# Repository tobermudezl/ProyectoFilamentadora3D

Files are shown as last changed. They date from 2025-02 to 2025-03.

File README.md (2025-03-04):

# ProyectoFilamentadora3D
Proyecto para la materia de Taller de Ingenieria Electronica.

# Integrantes 
Tomás Bermudez Lozano         | tobermudezl@unal.edu.co 

Juan Esteban Martinez Leon    | jumartinezle@unal.edu.co

Brayan Santiago Celi Almanza  | bceli@unal.edu.co

Johan Steven Ruiz Arango      | joruizar@unal.edu.co

# Descripción

Nuestro Proyecto tiene como fin de usar plastico reciclado filetiado (crear tiras homogeneas de plastico PET) por el usuario con el fin de crear filamento 3D con un prototipo economico y rentable para quienes quieran idearlo. Principalmente fue pensado para un consumo y reutilizacion eficaz de nuestros desechos plasticos. Los mismos desechos que se demoran al rededor de 300 o 400 años en descomponerse completamente. Aprovechando ese "problema" podemos verlo como una solucion eficaz para crear objetos en plastico resistentes, duraderos y amigables con el medio ambiente. Es un prototipo que tiene planeado ser implementado cerca de las salas con impresoras 3D con el fin que loe estudiantes puedan usar sus propias botellas plasticas recicladas y previamente fileteadas para poder ser introducidas por el prototipo y previamente usar el filamento 3D para sus proyectos.

# Problematica 

En Bogotá, la situación de los residuos plásticos es un desafío que afecta a todos. A medida que la ciudad crece y se urbaniza, también lo hacen los desechos plásticos, los cuales terminan, en su mayoría, en vertederos, ríos o incluso en las calles, generando problemas de contaminación que afectan la salud y el bienestar de los bogotanos. Aunque se han realizado esfuerzos por mejorar la gestión de residuos, todavía muy poco de lo que se produce se recicla correctamente, lo que agrava la situación y contribuye al cambio climático.
Por otro lado, la impresión 3D, que está ganando terreno en Bogotá, ofrece un sinfín de posibilidades en áreas como la educación, la construcción y la innovación tecnológica. Sin embargo, esta tecnología depende de filamentos plásticos, los cuales, en su mayoría, provienen de materiales nuevos, lo que continúa alimentando la demanda de recursos no sostenibles y aumentando el impacto ambiental. Aunque existen algunas alternativas de reciclaje, las tecnologías actuales para convertir los plásticos en nuevos productos no se han masificado por su alto costo y lo complejas que son de implementar. Es aquí donde surge una gran oportunidad: crear soluciones innovadoras que no solo ayudan a reducir los residuos plásticos, sino que también promuevan un uso más responsable de estos materiales, especialmente en áreas como la impresión 3D. Imaginemos una máquina capaz de transformar los plásticos que generamos en filamentos reciclados que puedan ser utilizados nuevamente para crear productos. Esta máquina no solo ayudaría a disminuir la cantidad de plásticos que terminan en vertederos, sino que también contribuiría a crear un ciclo de reutilización, donde los plásticos reciclados puedan tener una nueva vida, reduciendo la necesidad de plásticos vírgenes.
El agregado de un sistema de monitoreo en tiempo real permitiría controlar el proceso de reciclaje, asegurando que el filamento reciclado cumpla con los estándares necesarios para su uso en impresión 3D. Esto garantizaría que, incluso con plásticos reciclados, se mantuviera la calidad y funcionalidad del material. Implementar esta solución en Bogotá tendría múltiples beneficios. Por un lado, ayudaría a disminuir la cantidad de plástico desperdiciado que afecta tanto al medio ambiente como a la calidad de vida de los ciudadanos. Además, al reutilizar estos materiales, contribuiremos al cuidado del entorno y a reducir el impacto ambiental de la ciudad. Pero no solo eso, también abriría nuevas oportunidades de negocio, generando empleo en áreas como el reciclaje y la producción de materiales ecológicos. De esta manera, Bogotá podría fortalecer su compromiso con la sostenibilidad y avanzar hacia un futuro más verde y responsable.
Con proyectos como este, Bogotá podría dar un gran paso hacia un modelo más sostenible, no solo para enfrentar los problemas de los plásticos, sino para transformar la ciudad en un referente de innovación ambiental. Al integrar tecnologías como el reciclaje inteligente y la producción de filamentos reciclados, podríamos crear una economía más circular, generar empleo y, lo más importante, mejorar la calidad de vida para todos los bogotanos

# Objetivos 

Desarrollar un prototipo de filamentadora con método de extrusión sostenible a partir de residuos plásticos PET, que integre un sistema de monitoreo en tiempo real basado en IoT para garantizar la calidad del filamento producido, contribuyendo a la economía circular y la sostenibilidad ambiental.

# Objetivos Especifico

..* Diseñar el prototipo de la filamentadora con sistema de extrusión para el reciclaje de plásticos PET. 
..* Implementar un sistema de monitoreo en tiempo real mediante sensores IoT para la supervisión de la temperatura
..* Evaluar la calidad del filamento producido en términos de uniformidad, resistencia y viabilidad para la impresión 3D.
..* Desarrollar una interfaz gráfica para la visualización remota de los datos obtenidos por los sensores. 
..* Promover la conciencia ambiental sobre la reutilización de residuos plásticos a través de la demostración y divulgación del prototipo.

# Cronograma

![alt text]()

# Poster
![Poster]

# Producto Final

![Video Producto Final]

# Palabras Claves

Prototipos, Plastico reciclado, filamentadora, universidad, PET, plastico, reciclaje, medio ambiente.

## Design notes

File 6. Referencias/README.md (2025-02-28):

# Planteamiento de la Idea 

[Idea de la Filamentadora 3D](https://youtu.be/36BITwMVMGE?si=6mY6h9IGPmX1kqub)

Este fue el primer video que vimos como idea inicial, sabiendo que nuestro prototipo no se guiaria en todo lo que vimos, si no que es la idea principal.

# Videos para saber cosas que no teniamos ni idea de hacer 

[Como usar un motor paso a paso con ESP32](https://www.youtube.com/watch?v=MP3kUJ6SFCQ)

[Conectarlo con wifi el funcionamiento del motor paso a paso](https://www.youtube.com/watch?v=ysoVaclMy9Y)

[Motor PASO A PASO con ULN2023A Driver](https://www.youtube.com/watch?v=wLdFx4Kgc4M)

# Esquemas de conexion

## Esquema de conexion del sensor de temperatura DS18B20 con el microcontrolador ESP32

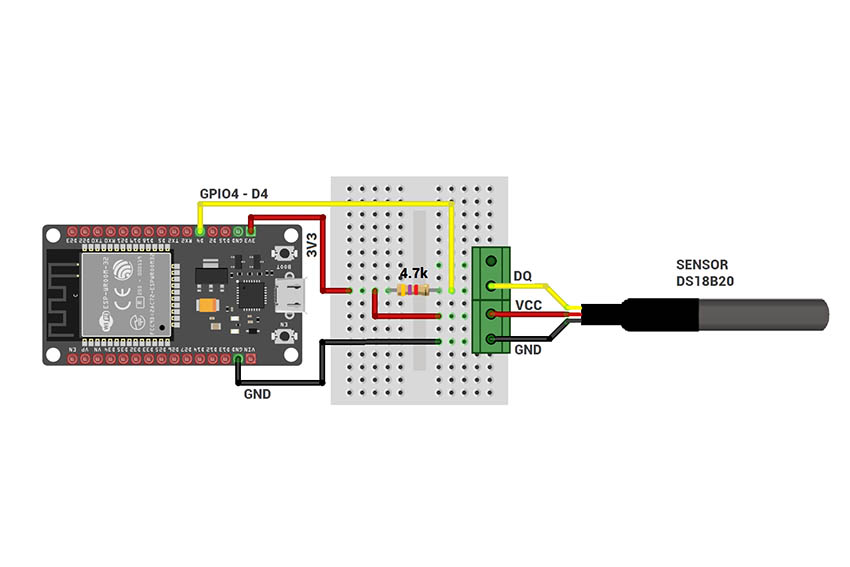
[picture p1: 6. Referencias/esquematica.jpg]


## PinOUT de ESP32 WROOM DEVKITV1

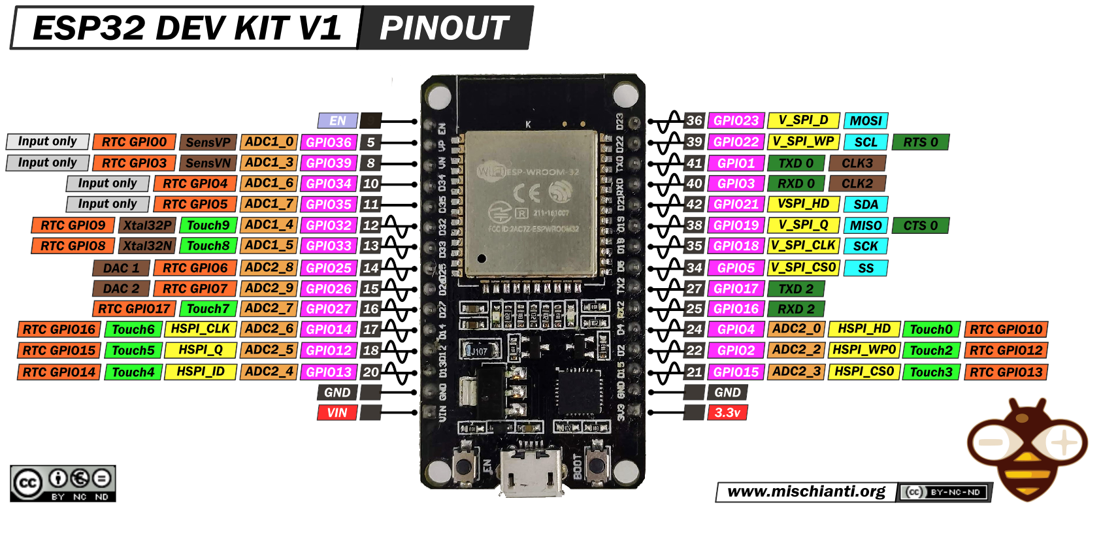
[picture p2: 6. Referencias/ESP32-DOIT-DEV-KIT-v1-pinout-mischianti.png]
esp32


## Conexion del LM7805

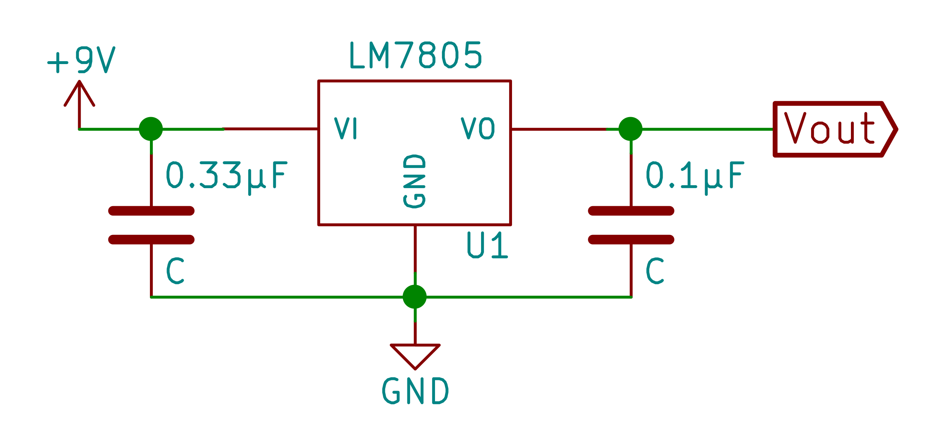
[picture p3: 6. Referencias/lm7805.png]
adap


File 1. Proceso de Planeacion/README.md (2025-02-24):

# Requerimientos

En esta parte comenzamos a pensar lo que queremos como proyecto final, nuestra idea principal de que queremos que nuestro prototipo haga, calcule, muestre, informe. Queremos que sea intregado con IoT porque es algo muy loco que nos enseño el Profe Johnny desde la primera clase. 

En el siguiente link se podra observar el PDF donde estan todas estas informaciones a detalle :) [REQUERIMIENTOS PRESENTACION](https://github.com/tobermudezl/ProyectoFilamentadora3D/blob/main/1.%20Proceso%20de%20Planeacion/Requerimientos.pdf)
# Diagrama de Flujo
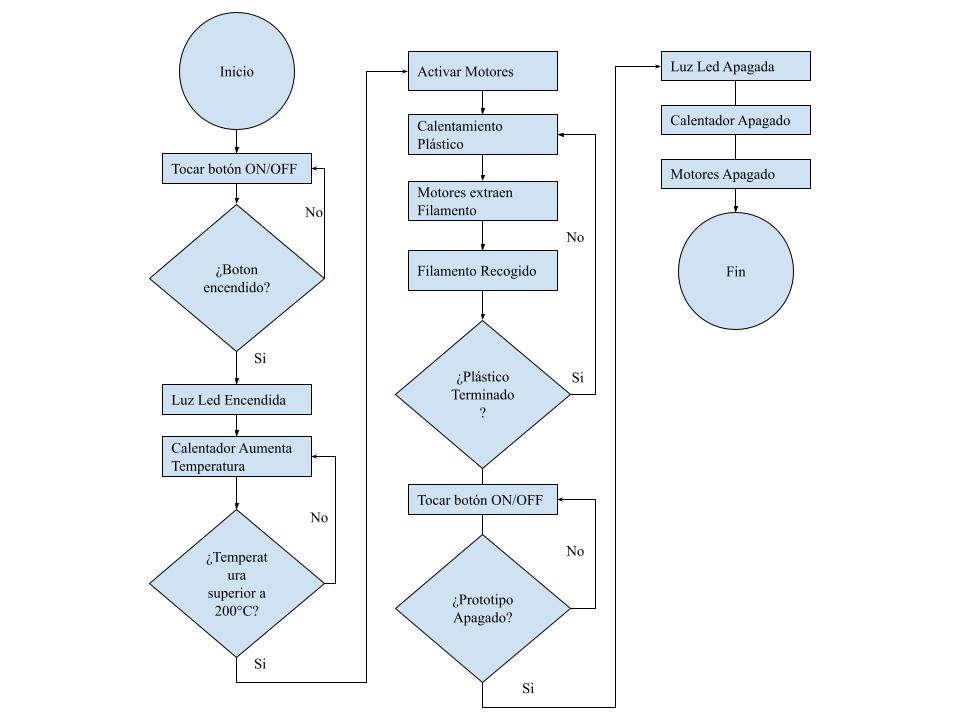
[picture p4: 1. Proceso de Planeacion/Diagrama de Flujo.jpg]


# Diagrama de Caja Negra - Sin tecnologia

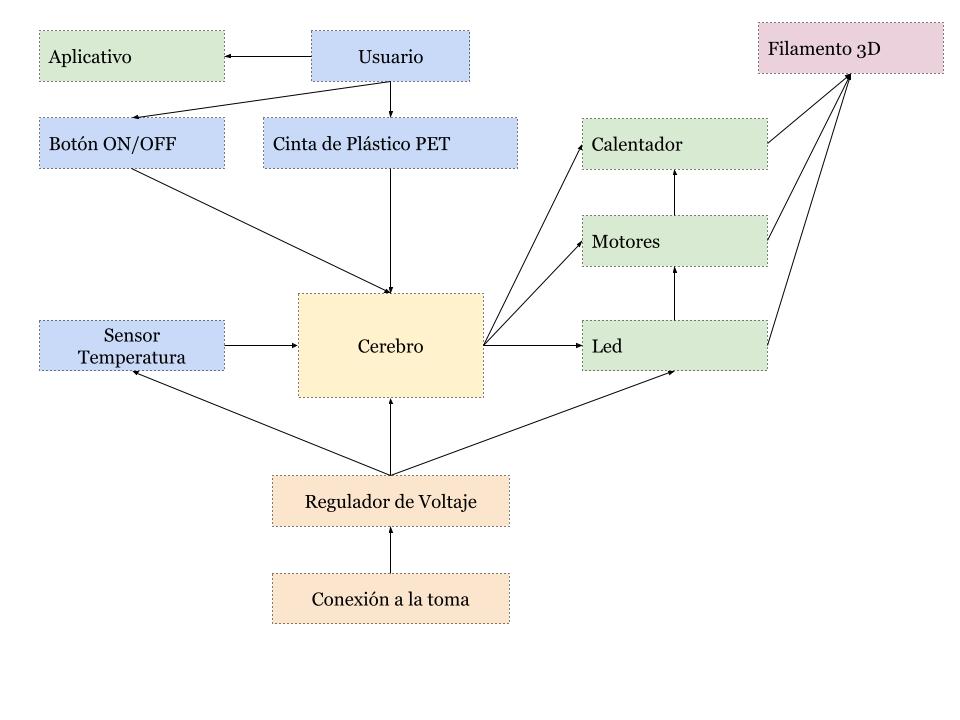
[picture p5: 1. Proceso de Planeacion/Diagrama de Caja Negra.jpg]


# Lista de Materiales

| **Material** | **Cantidad**  | 
| --- |:---:|
| Motores PASO A PASO28BYJ8 | 2 |  
| ULN2003A | 2 | 
| Condensadores de 10mf | 2 | 
| Resistencia de 4.7K ohm | 1 |  
| ESP32 DEV KIT V1 DOIT | 1 |
| Resistencia ceramica 40W | 1 |
| Parte calentador plastico | 1 |
| Led Verde | 1 |
| Resistencia  520 ohm | 1 | 
| LM7805 Regulador Voltaje | 1 |
| Cables o Jumpers | |

# Diagrama de Caja Negra - Con tecnologia

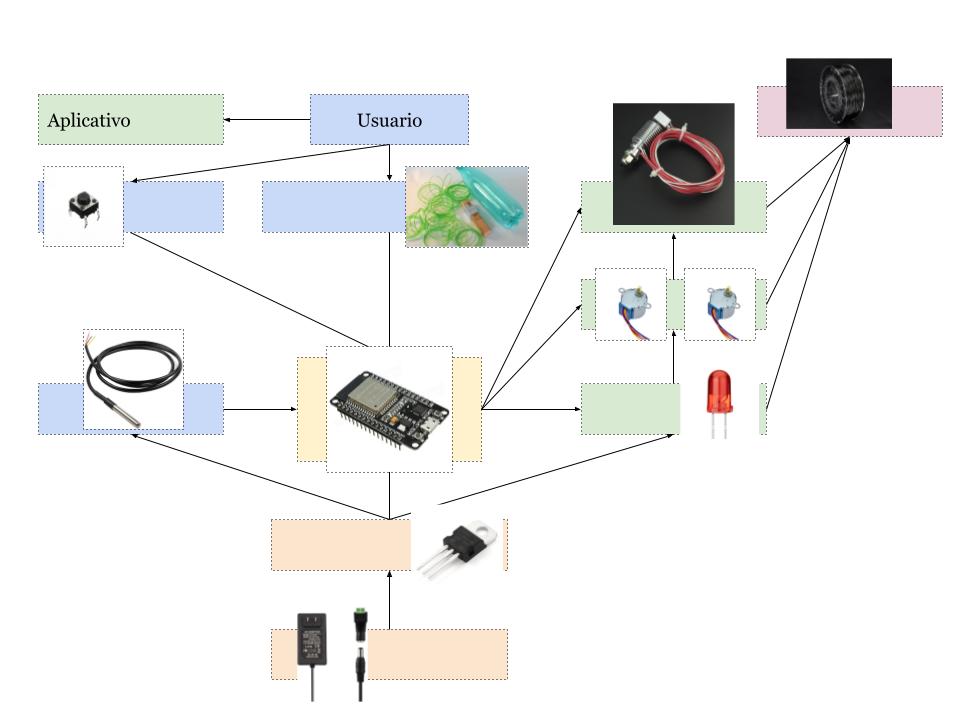
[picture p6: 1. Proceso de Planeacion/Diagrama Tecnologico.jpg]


# Paso a la fase 2

Despues de todo planificado pasamos a la parte dos del proyecto.

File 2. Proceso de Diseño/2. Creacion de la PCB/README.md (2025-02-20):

#  Informacion de la PCB

Una PCB de 9x9, una capa, tarjeta de fibra, antisolder, serigrafia.

Se ponen en esta carpeta las librerias usadas, los archivos completos del proyecto en KiCad.

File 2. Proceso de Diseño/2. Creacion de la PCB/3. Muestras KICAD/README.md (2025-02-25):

# Muestras Rapidas de Archivos KICAD

Primero tenemos el esquematico completo en pdf : [Esquematico](https://github.com/tobermudezl/ProyectoFilamentadora3D/blob/main/2.%20Proceso%20de%20Diseño/2.%20Creacion%20de%20la%20PCB/3.%20Muestras%20KICAD/esquematico.pdf)

La foto del ruteo de la PCB

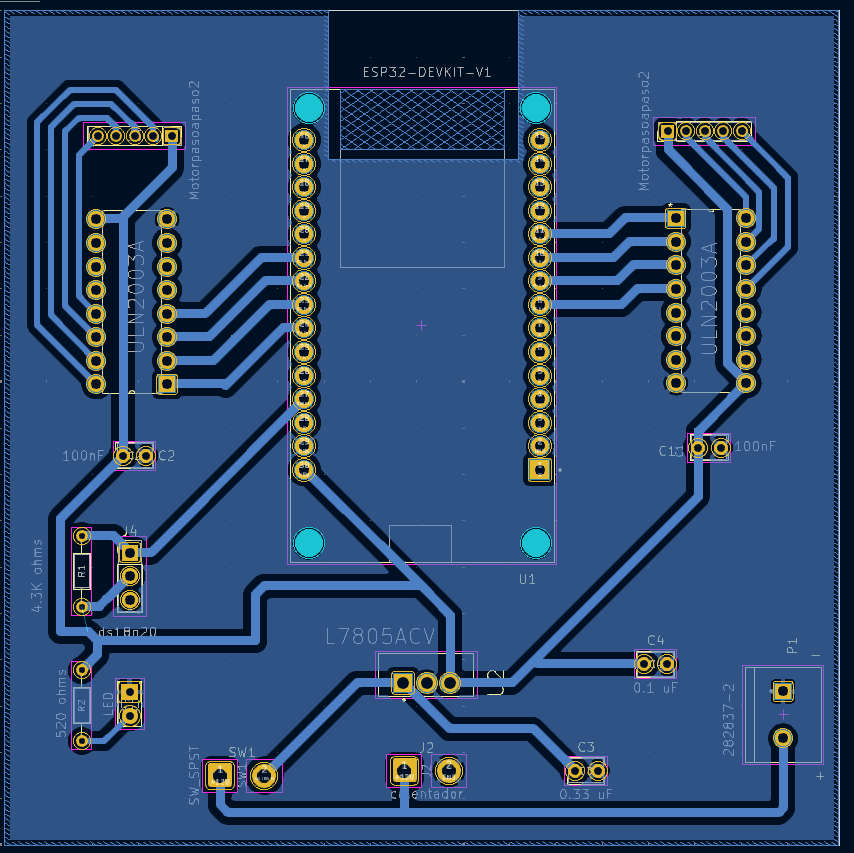
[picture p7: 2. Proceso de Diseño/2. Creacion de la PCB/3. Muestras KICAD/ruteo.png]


Y la foto de como se veria el modelo en version 3D

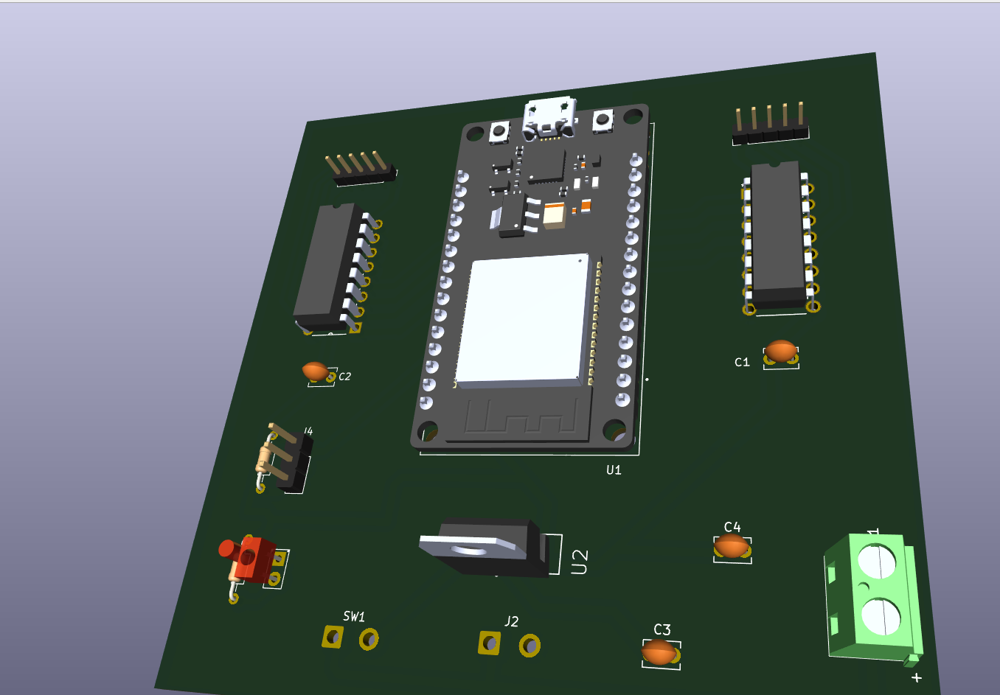
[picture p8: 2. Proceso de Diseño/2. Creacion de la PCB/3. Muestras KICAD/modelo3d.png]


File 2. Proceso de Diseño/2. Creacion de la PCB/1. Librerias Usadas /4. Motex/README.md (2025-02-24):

# Librerias de MOTEX

Incluye el archivo .kicad_sym, .step y .kicad_mod

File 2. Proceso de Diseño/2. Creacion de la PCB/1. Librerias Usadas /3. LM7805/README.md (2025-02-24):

# Librerias de LM7805 

Incluye el archivo .kicad_sym, .step y .kicad_mod

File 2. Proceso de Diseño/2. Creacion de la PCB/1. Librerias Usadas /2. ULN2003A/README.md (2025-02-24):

# Librerias de ULN2003A 

Incluye el archivo .kicad_sym, .step y .kicad_mod

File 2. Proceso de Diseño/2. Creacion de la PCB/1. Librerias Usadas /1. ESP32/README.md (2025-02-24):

# Librerias de ESP32 

Incluye el archivo .kicad_sym, .step y .kicad_mod

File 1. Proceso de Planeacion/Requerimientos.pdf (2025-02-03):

# REQUERIMIENTOS

## GRUPO 2

# Situación problema

La creciente utilización de plásticos de un solo uso, que en su mayoría no son reciclados adecuadamente, termina acumulándose en rellenos sanitarios como el de Doña Juana en Bogotá. Este relleno recibe alrededor de 300 toneladas de basura, de las cuales aproximadamente el 40 % corresponde a plásticos.

Nuestro prototipo está diseñado para aprovechar estos plásticos, específicamente el PET (#1), transformándolos en filamento para impresoras 3D. Este filamento permitirá la impresión de objetos que fomenten el reciclaje individual, promoviendo así la reutilización de plásticos de un solo uso y contribuyendo a una gestión más sostenible de los residuos.

# Flujo de Proceso

Proceso Previo: Antes de utilizar la máquina, el usuario debe triturar el plástico PET. Esto puede realizarse con herramientas accesibles, como una licuadora convencional, asegurándose de que los fragmentos sean lo suficientemente pequeños para ser procesados por el sistema.

# Flujo de Proceso

Etapas del Proceso:

1. Entrada: Se introduce plástico triturado por el usuario en el sistema a través de una tolva o compartimiento diseñado para este propósito.
2. Fusión: El plástico es calentado hasta alcanzar la temperatura ideal para su fundición, evitando la degradación del material y preservando su calidad.
3. Extrusión: El material fundido es moldeado mediante un cabezal de extrusión, formando un filamento uniforme con el diámetro requerido.
4. Enfriamiento: El filamento extruido pasa a través de un sistema de enfriamiento controlado para solidificarse sin deformaciones.
5. Enrollamiento: El filamento enfriado es automáticamente enrollado en bobinas, asegurando un almacenamiento práctico y listo para su uso en impresoras 3D.

# Funcionales

Procesamiento de plásticos: Debe fundir el PET triturado y moldearlo en filamentos de un diámetro adecuado para impresoras 3D.
Producción de filamento: El sistema debe tener el grosor del filamento para asegurar compatibilidad con estándares de impresoras 3D. Al igual debe embobinar el filamento producido para facilitar su uso.
Soporte para impresión 3D: Los filamentos producidos deben ser compatibles con las impresoras 3D más comunes en el mercado. Igualmente debe permitir la creación de objetos reutilizables o piezas relacionadas con el reciclaje. Monitoreo y reporte: El sistema debe permitir monitorear la temperatura y el correcto funcionamiento, al igual de poder dar un reporte completo.

# No funcionales

Eficiencia Energética: El sistema debe optimizar el consumo de energía durante todo el proceso.
Facilidad de Uso: La operación del sistema debe ser intuitiva y accesible para usuarios con diferentes niveles de experiencia, incluso sin conocimientos técnicos avanzados.De la misma forma la interfaz debe incluir instrucciones claras y herramientas automatizadas para reducir la intervención manual.
Portabilidad: El sistema debe tener un diseño compacto y modular, facilitando su transporte e instalación en distintos lugares, como centros de reciclaje comunitarios o pequeñas empresas.
Seguridad: Advertencias del uso del prototipo para evitar quemaduras, malos usos, y sus especificaciones para poder darle un manejo completo.

# No funcionales

Materiales Accesibles: El diseño del sistema debe priorizar componentes y materiales que sean fáciles de conseguir en el mercado local y que no encarezcan su producción. Siempre que sea posible, debe incluir materiales reciclados o reutilizables en su construcción.
Durabilidad: El sistema debe estar construido con materiales resistentes al desgaste, garantizando una vida útil prolongada incluso bajo condiciones de uso continuo.
Bajo Coste de Producción: Los costos asociados al desarrollo y operación del sistema deben mantenerse bajos para asegurar su viabilidad económica. Esto incluye el uso eficiente de recursos, la optimización del diseño y la reducción de desperdicios durante el proceso de fabricación.

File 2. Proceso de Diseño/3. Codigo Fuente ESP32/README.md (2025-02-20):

# Codigo Fuente del programa principal

Se adjuntaran los codigos de prueba y el main completo

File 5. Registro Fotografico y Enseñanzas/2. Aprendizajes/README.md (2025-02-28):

# Reflexión del Proceso de Aprendizaje

Como grupo, hemos vivido un proceso de aprendizaje donde la autonomía y el acompañamiento del profesor Johnny jugaron un papel fundamental. A lo largo del camino, enfrentamos diversos errores en diferentes aspectos, desde la planificación hasta la implementación. Cada equivocación fue una oportunidad para mejorar, buscando soluciones de forma colaborativa, investigando por nuestra cuenta y con el apoyo del profesor.

Entendimos que cometer errores es parte esencial del aprendizaje, ya que nos permitió fortalecer nuestros conocimientos, desarrollar paciencia y crecer como equipo. Gracias a cada desafío superado, hoy somos mejores que cuando iniciamos, y nos llevamos la enseñanza de que los errores no son fracasos, sino pasos necesarios para alcanzar el aprendizaje.

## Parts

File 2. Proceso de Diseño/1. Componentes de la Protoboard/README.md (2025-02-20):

# Elementos usados para el prototipo

En nuestro proyecto usamos varios materiales :

El Calentador de plastico :

![alt]()

Motores Paso A Paso :

![alt]()

ULN2003A :

![alt]()

Resistencias :

![alt]()

LM7805 :

![alt]()

Capacitores 104 (100nF):

![alt]()

ESP32 DEVKIT V1 :

![alt]()

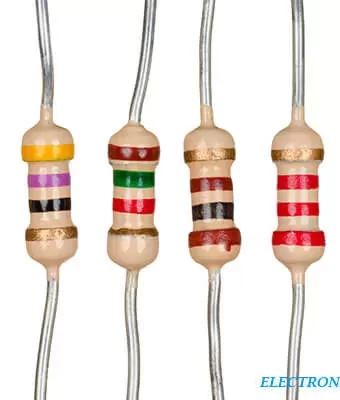
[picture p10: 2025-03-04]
2. Proceso de Diseño/1. Componentes de la Protoboard/res.webp

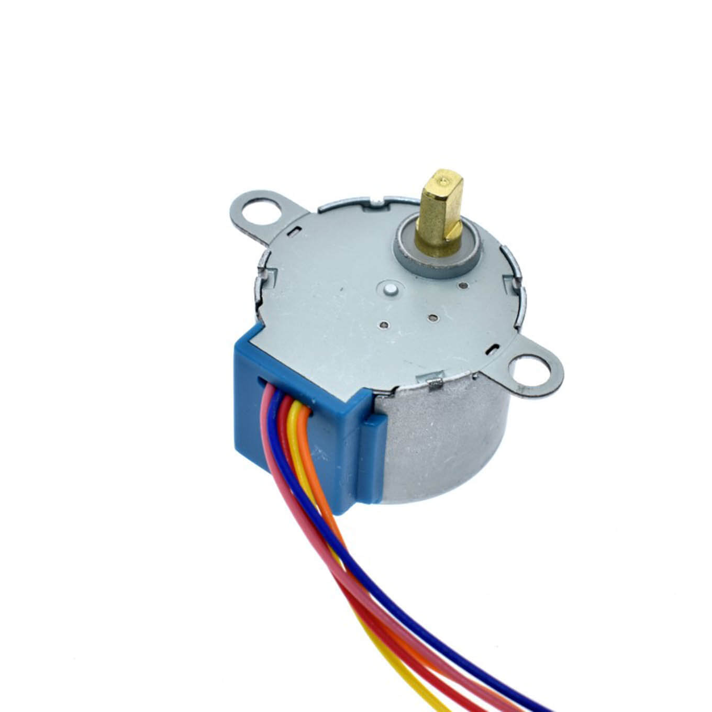
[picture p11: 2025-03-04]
2. Proceso de Diseño/1. Componentes de la Protoboard/motor.jpg

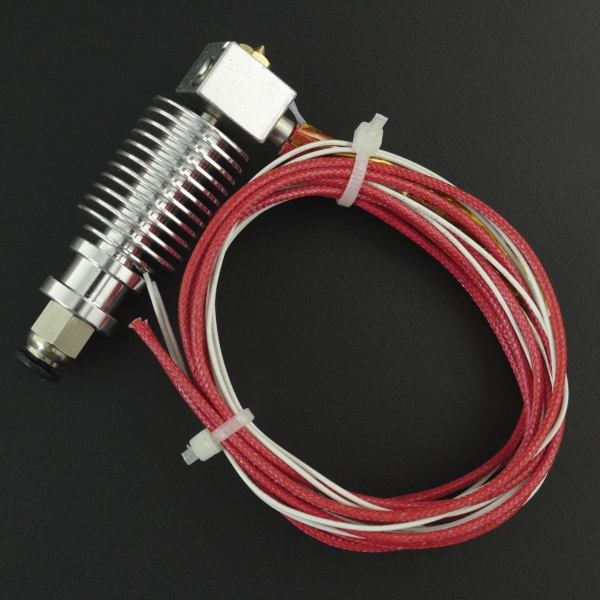
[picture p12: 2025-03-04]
2. Proceso de Diseño/1. Componentes de la Protoboard/extructor.jpg

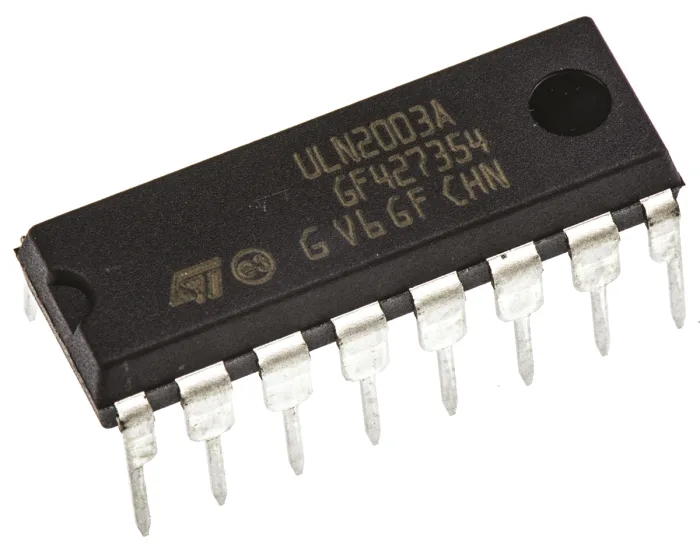
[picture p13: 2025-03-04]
2. Proceso de Diseño/1. Componentes de la Protoboard/uln2003a.webp

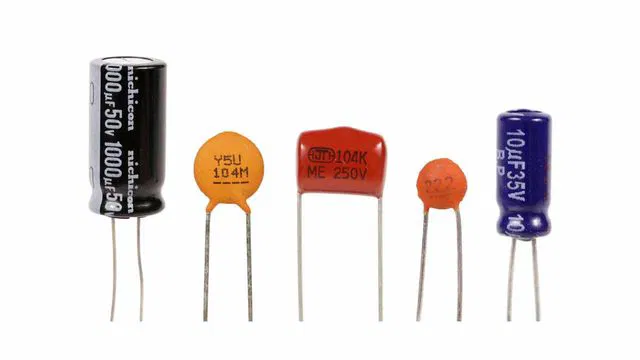
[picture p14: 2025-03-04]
2. Proceso de Diseño/1. Componentes de la Protoboard/capacitor.webp

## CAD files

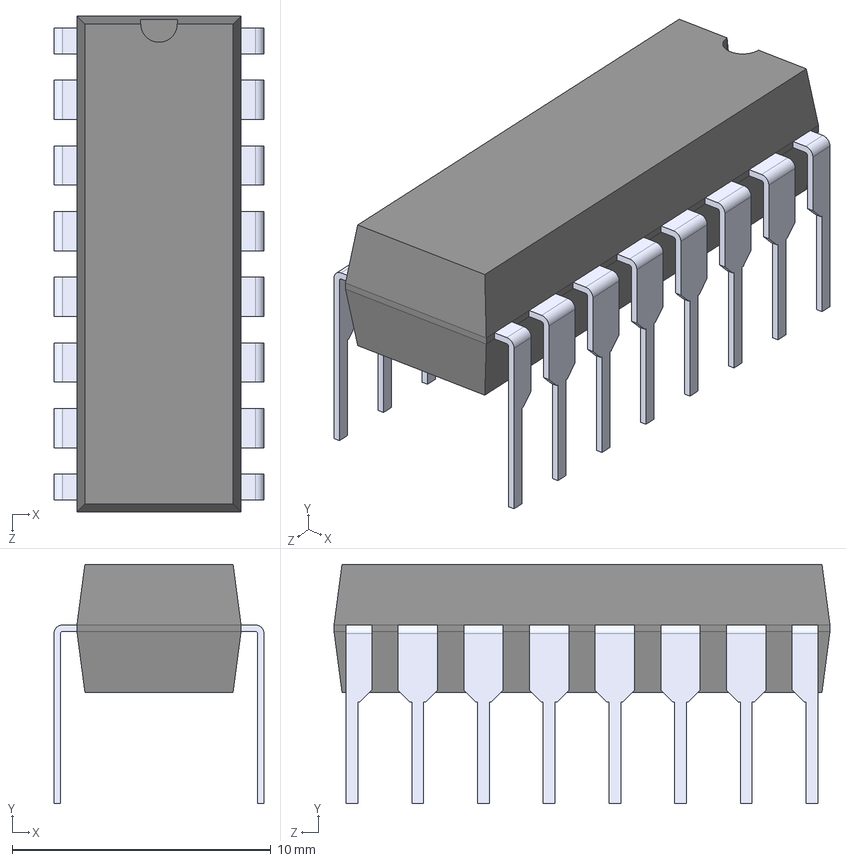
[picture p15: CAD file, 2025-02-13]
2. Proceso de Diseño/2. Creacion de la PCB/1. Librerias Usadas /2. ULN2003A/ULN2003A.step
8.12 x 9.26 x 19.2 mm

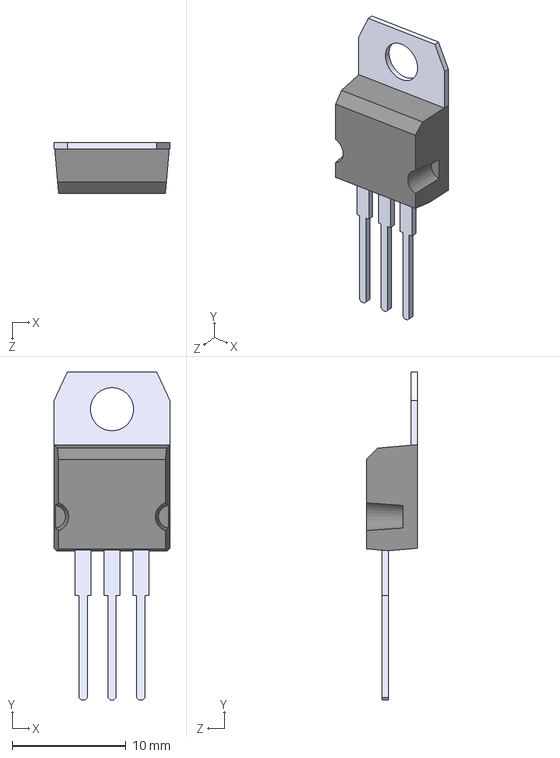
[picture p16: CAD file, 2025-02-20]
2. Proceso de Diseño/2. Creacion de la PCB/1. Librerias Usadas /3. LM7805/L7805ACV.step
10.2 x 28.9 x 4.50 mm

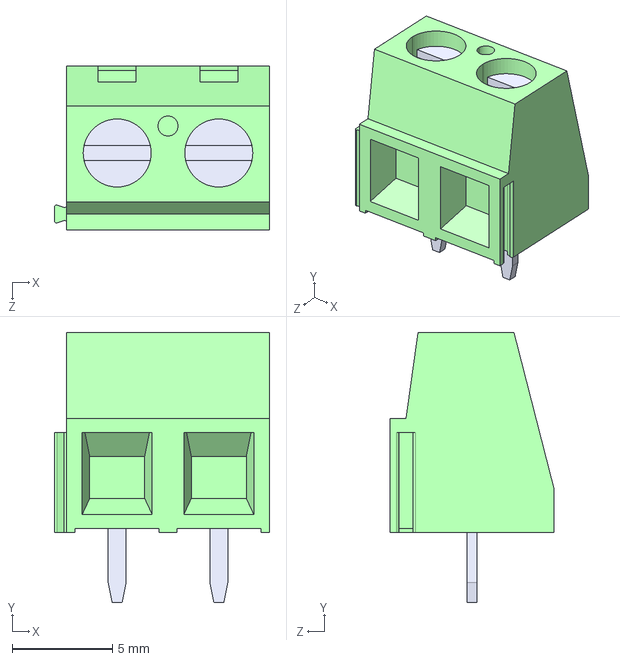
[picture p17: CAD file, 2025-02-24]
2. Proceso de Diseño/2. Creacion de la PCB/1. Librerias Usadas /4. Motex/282837-2.step
10.8 x 13.5 x 8.20 mm

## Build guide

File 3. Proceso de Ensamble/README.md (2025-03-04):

# Soldadura

Se soldaron todos los componentes en la PCB

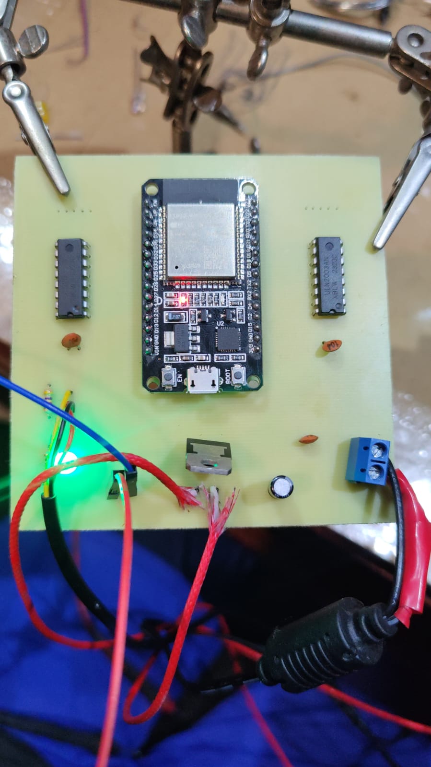
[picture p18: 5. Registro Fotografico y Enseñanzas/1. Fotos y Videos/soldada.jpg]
Soldadura


Se encontro un error de impresion de nuestra parte donde no se conecto bien una conexion, sin embargo solo se raspo un poco y se soldo con estaño

El esto de imagenes y videos de la soldadura estan en la carpeta [1. Fotos y Videos](https://github.com/tobermudezl/ProyectoFilamentadora3D/tree/main/5.%20Registro%20Fotografico%20y%20Enseñanzas/1.%20Fotos%20y%20Videos)

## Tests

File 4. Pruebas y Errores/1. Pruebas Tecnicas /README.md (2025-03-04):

# Proyecto: Pruebas y Mejoras en la Filamentadora

## Cambios y Mejoras Implementadas  

### Cambio de Driver: A8119 → ULN2003A  
Inicialmente usamos el driver **A8119**, pero tuvimos dificultades para hacerlo funcionar correctamente debido a la falta de documentación clara y problemas en la implementación. Después de varias pruebas, decidimos reemplazarlo por el **ULN2003A**, un driver más accesible y ampliamente utilizado para motores paso a paso pequeños. Este cambio nos permitió simplificar la conexión y el control del motor.  

### Cambio de Motores: NEFA → 28BYJ-48  
En las primeras pruebas, utilizamos motores **NEFA**, pero eran costosos y tenían un consumo de corriente mayor del esperado. Esto generó dificultades al usarlos con las fuentes de alimentación disponibles. Optamos por cambiarlos por los motores **28BYJ-48**, que son más económicos y compatibles con el **ULN2003A**. Aunque estos motores tienen menor torque, se ajustaron mejor a los requerimientos del proyecto.  

### Problemas con el Sensor de Temperatura DS18B20  
Uno de los mayores desafíos fue obtener lecturas correctas del sensor de temperatura **DS18B20**. Inicialmente, el sensor no enviaba datos o mostraba valores erróneos. Los principales errores encontrados fueron:  
- Falta de una resistencia pull-up de **4.7kΩ** en la línea de datos, lo que impedía la comunicación con el microcontrolador.  
- Uso de librerías incompatibles, que no permitían la correcta lectura del sensor.  
- Conexiones incorrectas en el circuito, lo que dificultaba la transmisión de datos.  

Tras múltiples pruebas, logramos obtener lecturas estables utilizando las librerías basicas

### Problemas con la Velocidad del Motor Paso a Paso  
Desde el inicio del proyecto, tuvimos dificultades para lograr que el motor se moviera a la velocidad deseada. Entre los problemas identificados estaban:  
- Uso de la función `delay()`, lo que afectaba el rendimiento y velocidad del motor.  
- Configuración incorrecta de la frecuencia de pasos, lo que generaba movimientos erráticos.  
- Uso de la librería `Stepper.h`, que no nos permitió un control preciso de la velocidad y aceleración.

Simplemente le damos un tiempo de descanso entre cada 90 grados

## Conclusiones  
Durante el semestre, enfrentamos varios problemas técnicos que nos obligaron a investigar, probar diferentes soluciones y mejorar nuestra comprensión del funcionamiento de los motores paso a paso y sensores. Aunque en algunos momentos fue complicado, logramos resolver los errores y mejorar el desempeño del prototipo.  

Este proyecto nos permitió aprender sobre la importancia de la documentación técnica, la depuración de código y la selección adecuada de componentes.

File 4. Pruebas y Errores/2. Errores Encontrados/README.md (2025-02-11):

#  Errores

## Primer Diagrama de Flujo demasiado complicado:

En este diagrama de flujo, pensamos en demasiadas cosas que son muy innovadoras, pero se nos iban de la idea principal del prototipo que es hacer el filamento 3D
[Diagrama de Flujo Fallido](https://github.com/tobermudezl/ProyectoFilamentadora3D/blob/main/4.%20Pruebas%20y%20Errores/2.%20Errores%20Encontrados/2.%20Diagrama%20Filamento%20con%20PET.pdf)

## El experimento con un calentador de pistola de silicona que al final fallo. 

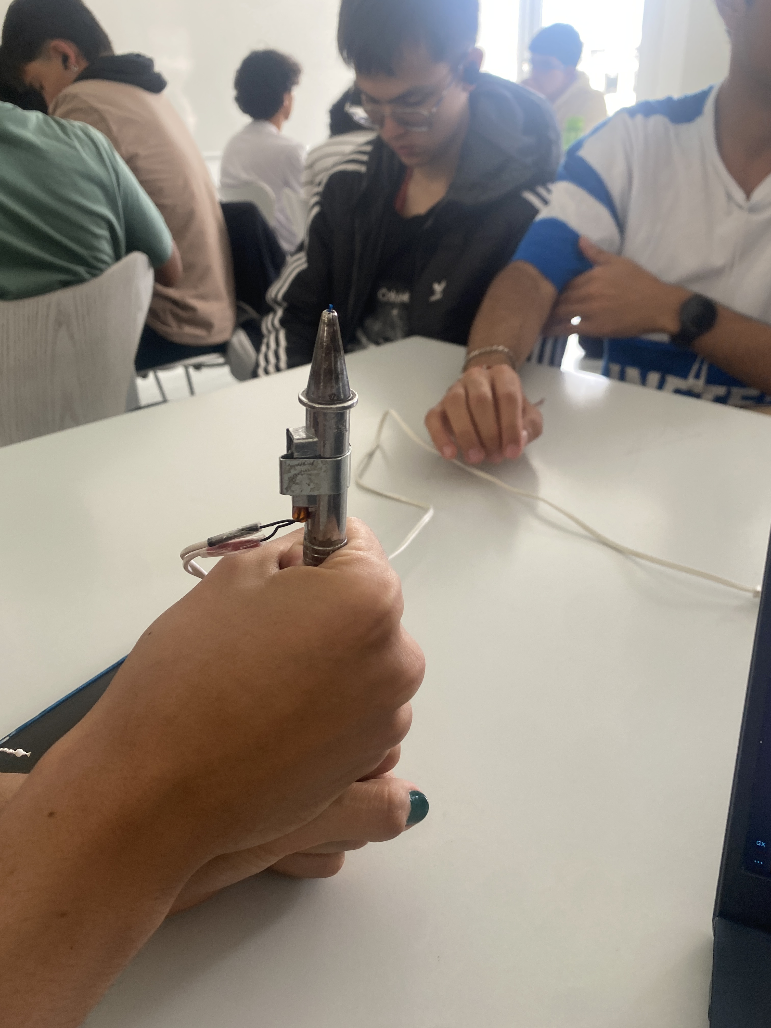
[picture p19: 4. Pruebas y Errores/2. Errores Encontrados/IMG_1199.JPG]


Nos quedo complicado encontrar una forma de añadir la otra resistencia ceramica al lado del calentador, de igual forma teniamos que usar voltaje a mas de 120V, algo que nos causa miedo por dañar algun componente.
Asumimos el costo de comprar un calentador en condiciones, para que nos podamos enfocar completamente en la electronica y los retos que conllevan las conexiones, soladura y creacion de la PCB

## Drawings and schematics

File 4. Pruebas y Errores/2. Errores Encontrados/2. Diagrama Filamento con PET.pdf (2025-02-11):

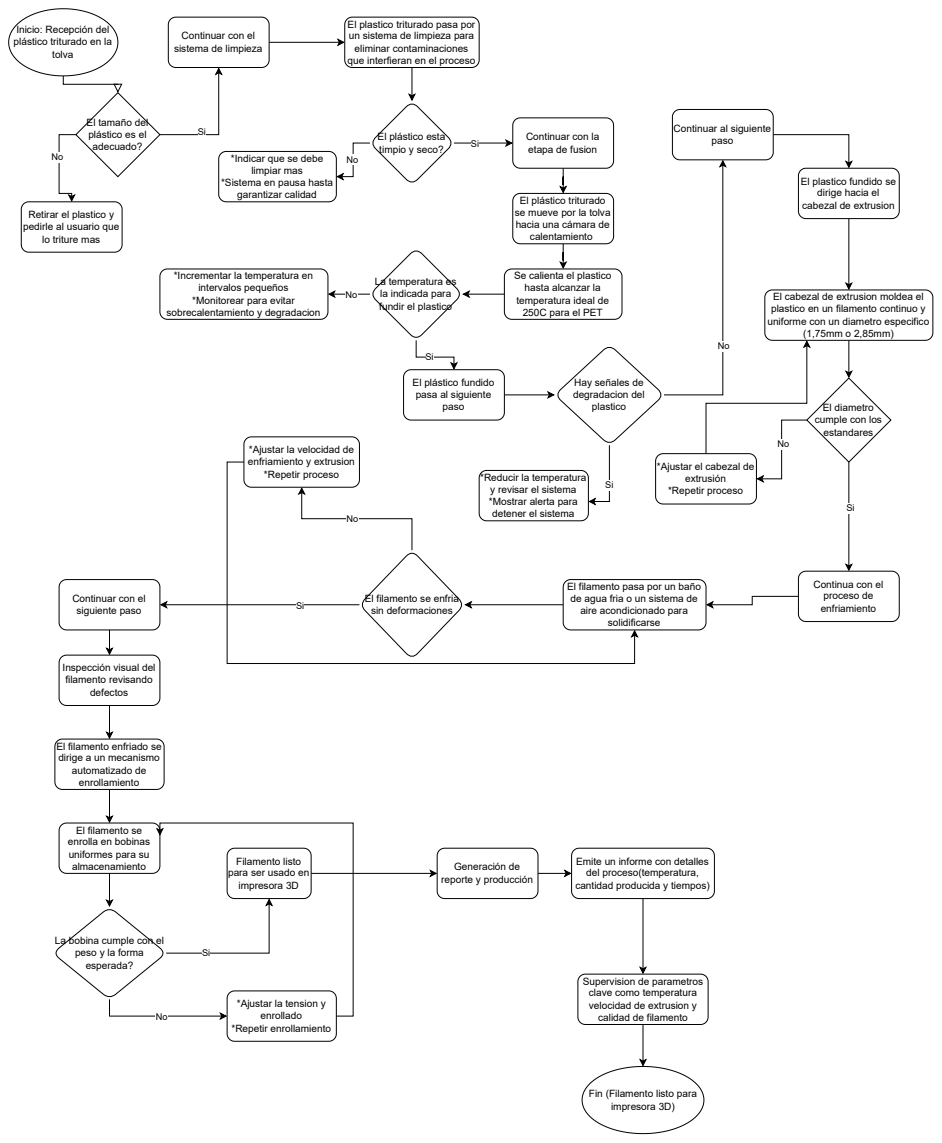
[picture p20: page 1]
garantizar calidad; El plástico triturado; paso; El filamento se enfria; sin deformaciones; Generación de reporte y producción; tolva

El plastico triturado pasa por
un sistema de limpieza para
eliminar contaminaciones
que interfieran en el proceso

Inicio: Recepción del
plástico triturado en la

Continuar con el
sistema de limpieza

El tamaño del
plástico es el
adecuado?

Continuar al siguiente

El plástico esta
timpio y seco?

Continuar con la
etapa de fusion

*Indicar que se debe
limpiar mas
*Sistema en pausa hasta

El plastico fundido se
dirige hacia el
cabezal de extrusion

Retirar el plastico y
pedirle al usuario que
lo triture mas

se mueve por la tolva
hacia una cámara de
calentamiento

*Incrementar la temperatura en
intervalos pequeños
*Monitorear para evitar
sobrecalentamiento y degradacion

Se calienta el plastico
hasta alcanzar la
temperatura ideal de
250C para el PET

La temperatura es
la indicada para
fundir el plastico

El cabezal de extrusion moldea el
plastico en un filamento continuo y
uniforme con un diametro especifico

El plástico fundido
pasa al siguiente
paso

Hay señales de
degradacion del
plastico

El diametro
cumple con los
estandares

*Ajustar la velocidad de
enfriamiento y extrusion
*Repetir proceso

*Ajustar el cabezal de
extrusión

*Reducir la temperatura
y revisar el sistema
*Mostrar alerta para
detener el sistema

El filamento pasa por un baño
de agua fria o un sistema de
aire acondicionado para
solidificarse

Continua con el
proceso de
enfriamiento

siguiente paso

Inspección visual del
filamento revisando
defectos

El filamento enfriado se
dirige a un mecanismo
automatizado de
enrollamiento

El filamento se
enrolla en bobinas
uniformes para su
almacenamiento

Filamento listo
para ser usado en
impresora 3D

Emite un informe con detalles
del proceso(temperatura,
cantidad producida y tiempos)

La bobina cumple con el
peso y la forma
esperada?

Supervision de parametros
clave como temperatura
velocidad de extrusion y
calidad de filamento

*Ajustar la tension y
enrollado
*Repetir enrollamiento

Fin (Filamento listo para
impresora 3D)

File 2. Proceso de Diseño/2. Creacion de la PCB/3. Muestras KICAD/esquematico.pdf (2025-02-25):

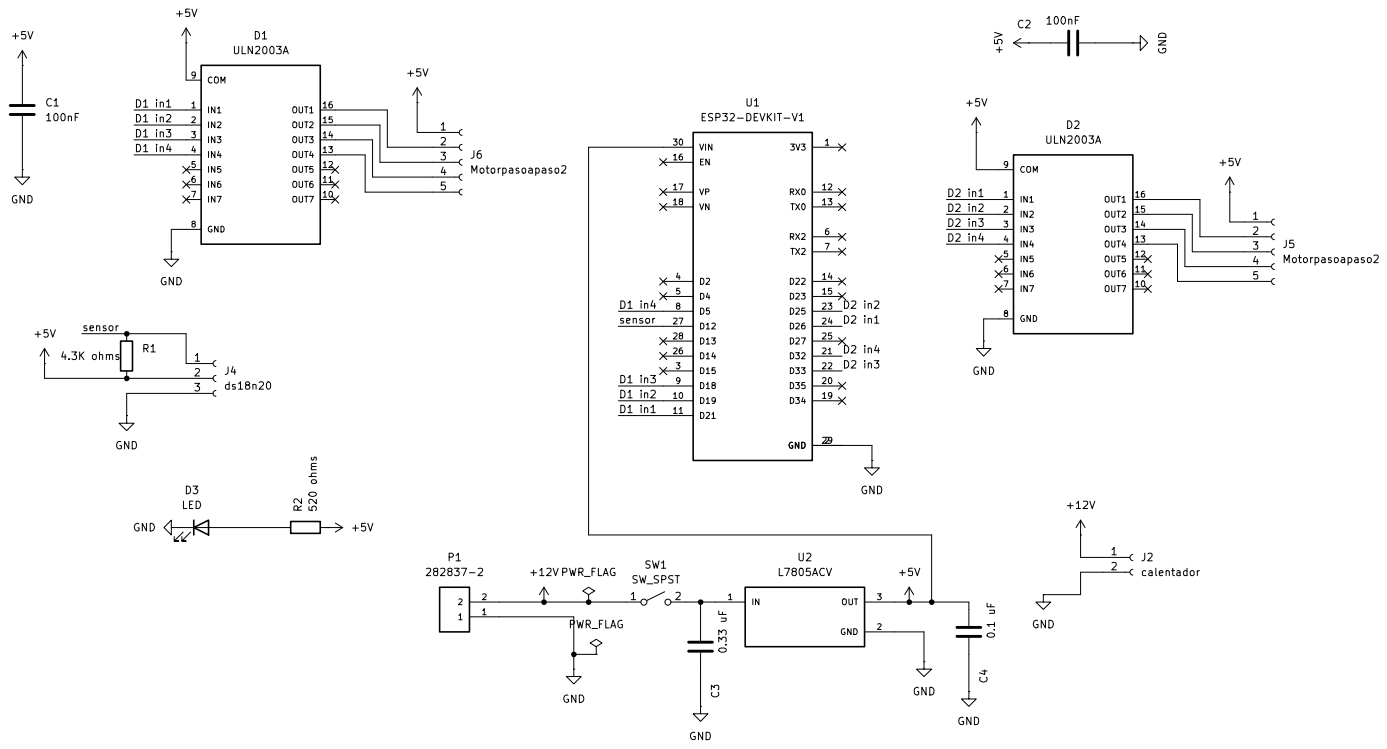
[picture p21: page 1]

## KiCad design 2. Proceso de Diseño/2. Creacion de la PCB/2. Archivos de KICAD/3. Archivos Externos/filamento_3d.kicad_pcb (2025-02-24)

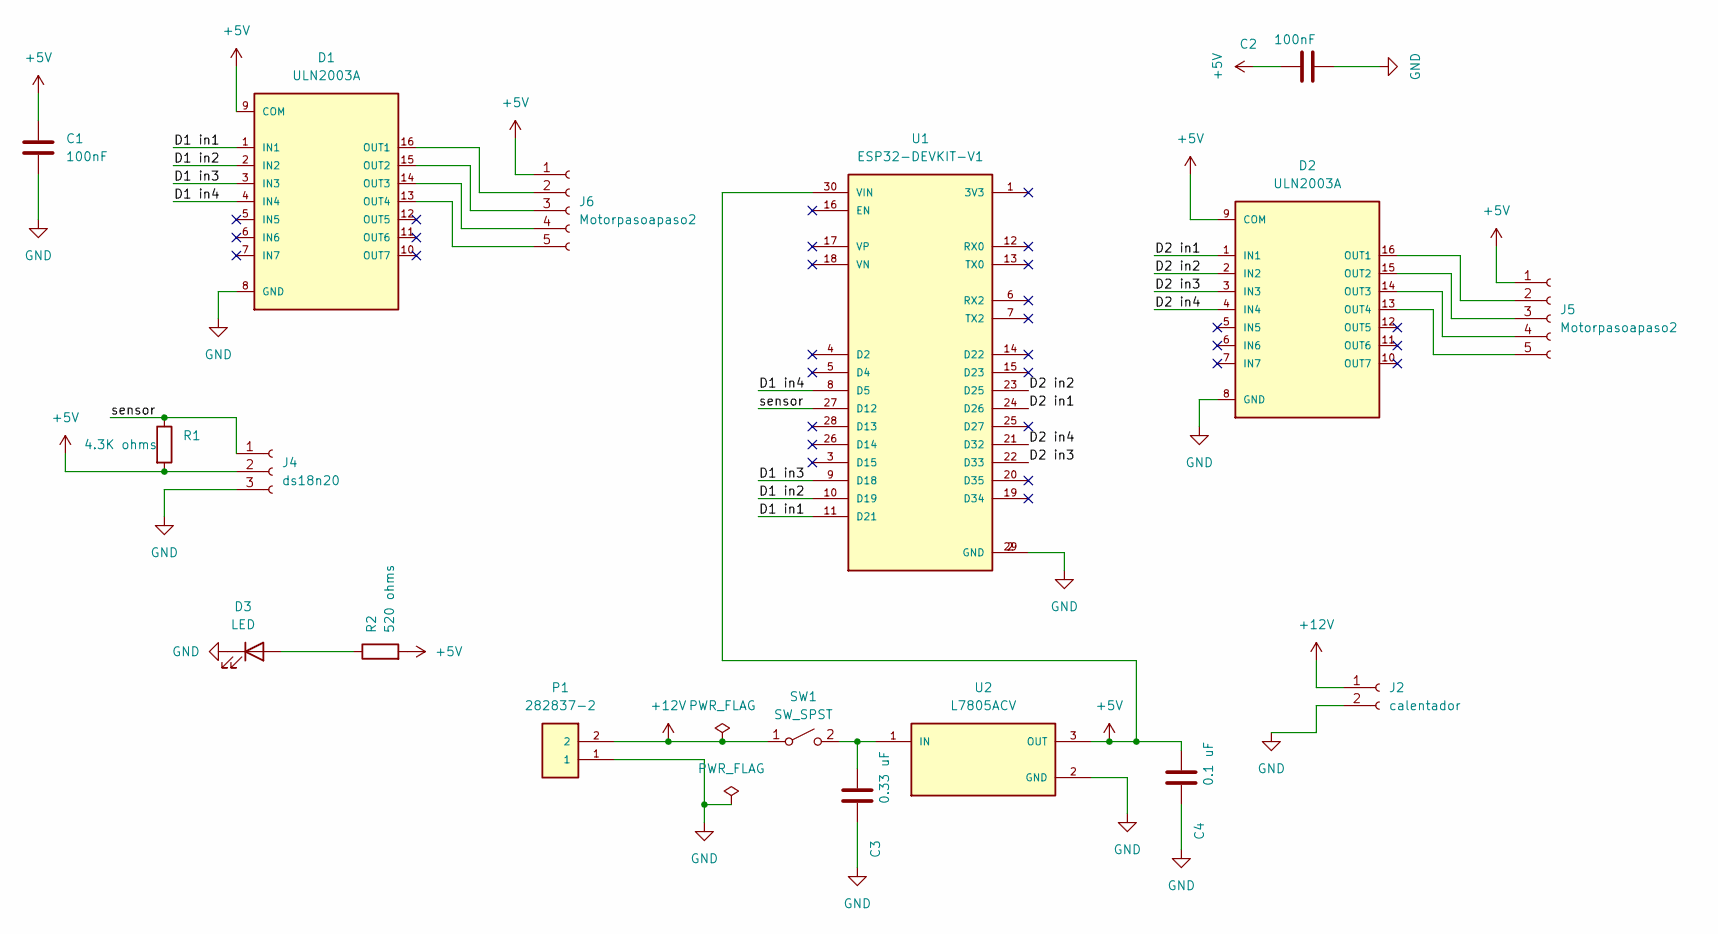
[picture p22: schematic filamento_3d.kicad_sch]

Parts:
C1, C2: 100nF; C_Disc_D3.8mm_W2.6mm_P2.50mm
C3: 0.33 uF; C_Disc_D3.8mm_W2.6mm_P2.50mm
C4: 0.1 uF; C_Disc_D3.8mm_W2.6mm_P2.50mm
D1, D2: ULN2003A; DIP254P762X445-16
D3: LED; LED_D2.0mm_W4.8mm_H2.5mm_FlatTop
J2: calentador; SolderWire-0.75sqmm_1x02_P4.8mm_D1.25mm_OD2.3mm
J4: ds18n20; PinHeader_1x03_P2.54mm_Vertical
J5, J6: Motorpasoapaso2; PinHeader_1x05_P2.00mm_Vertical
P1: 282837-2; TE_282837-2; PARTREV G3
R1: 4.3K ohms; R_Axial_DIN0204_L3.6mm_D1.6mm_P7.62mm_Horizontal
R2: 520 ohms; R_Axial_DIN0204_L3.6mm_D1.6mm_P7.62mm_Horizontal
SW1: SW_SPST; SolderWire-0.75sqmm_1x02_P4.8mm_D1.25mm_OD2.3mm
U1: ESP32-DEVKIT-V1; MODULE_ESP32_DEVKIT_V1; PARTREV N/A
U2: L7805ACV; TO254P460X1020X1945-3P

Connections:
+5V: C1.1, C2.1, C4.1, D1.9 (COM), D2.9 (COM), J4.2, J5.1, J6.1, R1.2, R2.2, U1.30 (VIN), U2.3 (OUT)
+12V: J2.1, P1.2, SW1.1 (A)
/D1 in1: D1.1 (IN1), U1.11 (D21)
/D1 in2: D1.2 (IN2), U1.10 (D19)
/D1 in3: D1.3 (IN3), U1.9 (D18)
/D1 in4: D1.4 (IN4), U1.8 (D5)
/D2 in1: D2.1 (IN1), U1.24 (D26)
/D2 in2: D2.2 (IN2), U1.23 (D25)
/D2 in3: D2.3 (IN3), U1.22 (D33)
/D2 in4: D2.4 (IN4), U1.21 (D32)
/sensor: J4.1, R1.1, U1.27 (D12)
GND: C1.2, C2.2, C3.2, C4.2, D1.8 (GND), D2.8 (GND), D3.1 (K), J2.2, J4.3, P1.1, U1.2 (GND), U1.29 (GND), U2.2 (GND)
unnamed: D1.16 (OUT1), J6.2
unnamed: D1.15 (OUT2), J6.3
unnamed: D1.14 (OUT3), J6.4
unnamed: D1.13 (OUT4), J6.5
unnamed: D2.16 (OUT1), J5.2
unnamed: D2.15 (OUT2), J5.3
unnamed: D2.14 (OUT3), J5.4
unnamed: D2.13 (OUT4), J5.5
unnamed: D3.2 (A), R2.1
unnamed: C3.1, SW1.2 (B), U2.1 (IN)

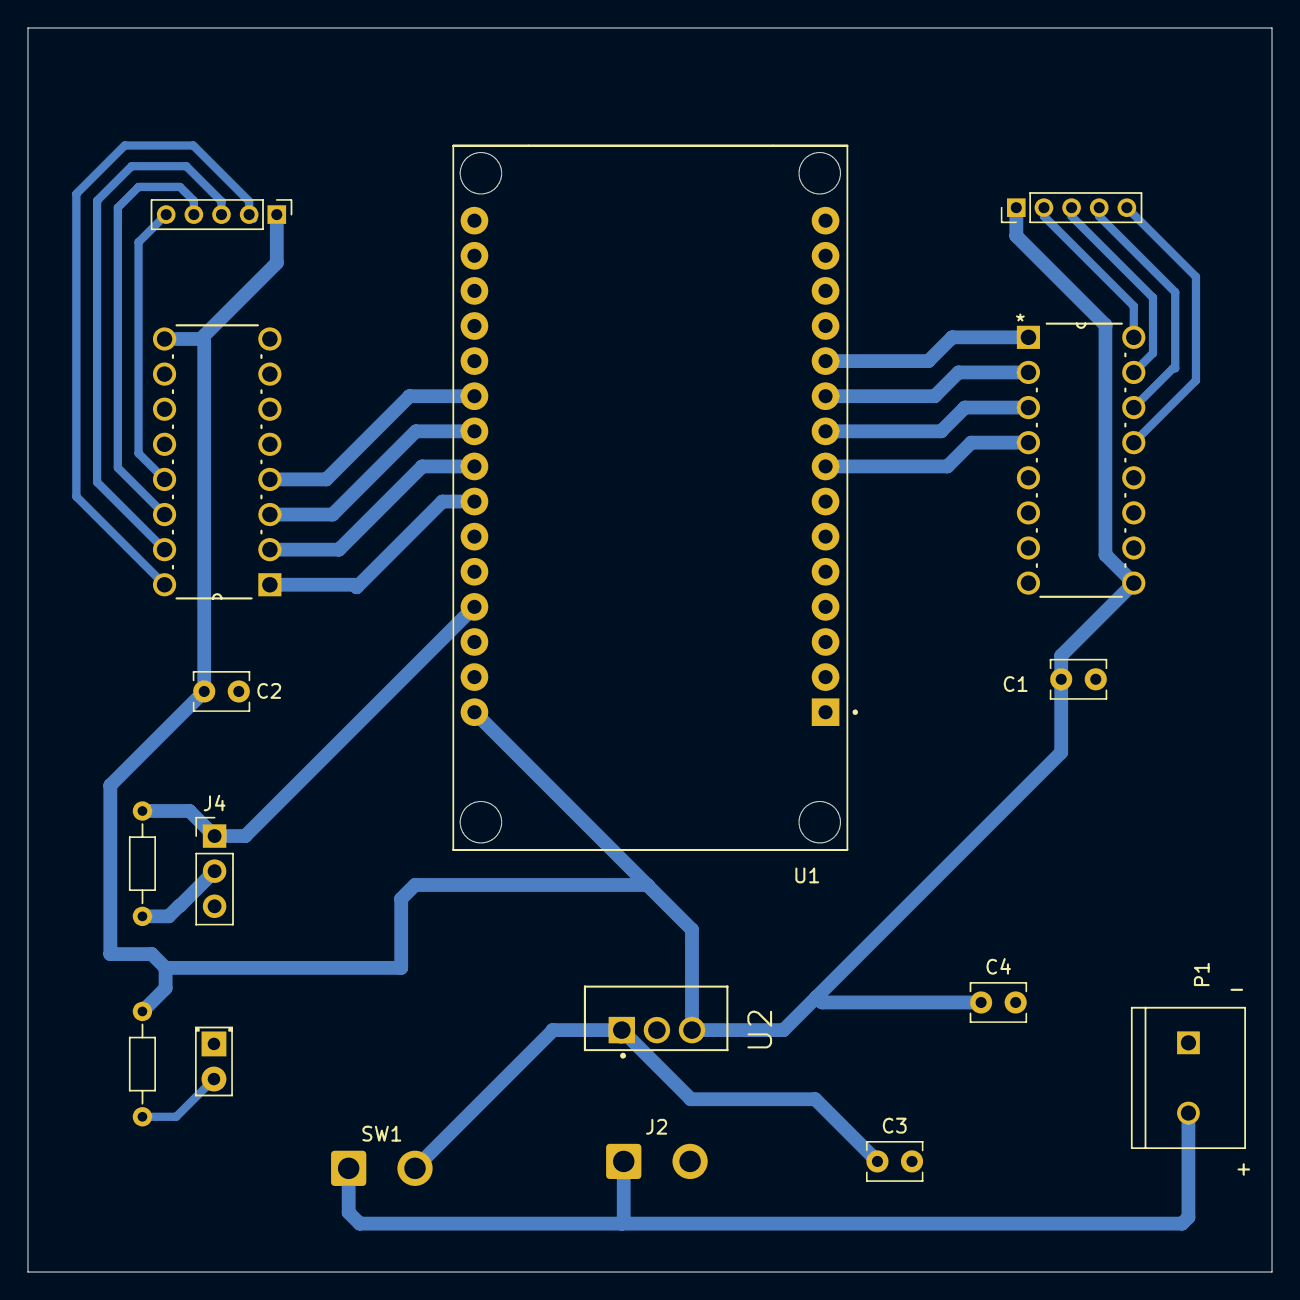
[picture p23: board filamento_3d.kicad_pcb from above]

Board: 2 copper layers, 90.0 x 90.0 mm, 17 parts (0 on the bottom side), 22 nets.

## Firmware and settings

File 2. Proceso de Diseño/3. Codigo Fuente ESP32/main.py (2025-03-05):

import machine
import onewire
import ds18x20
import time
from machine import Pin
import sys

# Configuración del sensor DS18B20
PIN_SENSOR = 12  # GPIO12
TEMP_MIN = 18  # 0% corresponde a 18°C
TEMP_MAX = 220  # Ajusta este valor según la temperatura máxima del dispositivo
TEMP_UMBRAL_ALTA = 100  # Temperatura máxima para activar motores
TEMP_UMBRAL_BAJA = 0  # Temperatura mínima para activar motores
PIN_LED = 2  # LED integrado en el ESP32

# Inicializar sensor
temp_sensor = machine.Pin(PIN_SENSOR)
ow = onewire.OneWire(temp_sensor)
ds = ds18x20.DS18X20(ow)

# Buscar sensores
roms = ds.scan()
if not roms:
    print("No se encontró ningún sensor DS18B20")
    while True:
        pass
print("Sensor DS18B20 encontrado:", roms)

# Definir los pines del ESP32 para controlar los drivers ULN2003
motor1_pins = [Pin(21, Pin.OUT), Pin(19, Pin.OUT), Pin(18, Pin.OUT), Pin(5, Pin.OUT)]
motor2_pins = [Pin(23, Pin.OUT), Pin(22, Pin.OUT), Pin(1, Pin.OUT), Pin(3, Pin.OUT)]
led = Pin(PIN_LED, Pin.OUT)

# Secuencia para el motor paso a paso (modo de media fase)
secuencia = [
    [1, 0, 0, 1],
    [1, 0, 0, 0],
    [1, 1, 0, 0],
    [0, 1, 0, 0],
    [0, 1, 1, 0],
    [0, 0, 1, 0],
    [0, 0, 1, 1],
    [0, 0, 0, 1]
]

# Función para mover un motor "n" pasos
def mover_motor(pins, pasos, delay=2):
    for _ in range(pasos):
        for sec in secuencia:
            for pin, val in zip(pins, sec):
                pin.value(val)
            time.sleep_ms(delay)

while True:
    ds.convert_temp()
    time.sleep_ms(750)
    temp = ds.read_temp(roms[0])

    if temp is None:
        print("Error al leer la temperatura")
        continue
    
    print(f"Temperatura: {temp:.2f}°C")
    
    # Leer entrada serial para comando manual
    if sys.stdin in select.select([sys.stdin], [], [], 0)[0]:
        comando = sys.stdin.read(1).strip()
        if comando == "M":
            print("Comando manual recibido: Activando motores")
            mover_motor(motor1_pins, 128)
            mover_motor(motor2_pins, 128)
            led.value(1)

    # Activar motores si la temperatura es mayor a 100°C o menor a 0°C
    if temp >= TEMP_UMBRAL_ALTA or temp <= TEMP_UMBRAL_BAJA:
        print("Temperatura fuera de rango seguro, activando motores")
        mover_motor(motor1_pins, 128)
        mover_motor(motor2_pins, 128)
        led.value(1)  # Encender LED de estado
    else:
        led.value(0)  # Apagar LED cuando no está activo
    
    time.sleep(1)
